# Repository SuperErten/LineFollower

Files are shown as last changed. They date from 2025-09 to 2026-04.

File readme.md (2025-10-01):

# LineFollower

lege repository die je als template kan gebruiken om een eigen repository te starten voor uw linefollower project

A description of my image


## specifications (Plan B)

microcontroller: ESP32 (Devkit V1)

motors: (50:1) micro metal gearbox HP 6V - pololu

h-bridge: DRV8833

sensors: QTR-8A

batteries: 18650 - 3.7x2V; 2.6A

wireless communication: See microcontroller

distance sensor - motors:

weight:

speed:

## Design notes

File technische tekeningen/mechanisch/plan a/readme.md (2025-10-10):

## Latest PCB design
<br />
Exported in DXF, 3D model (obj) and EASYEDA (json).

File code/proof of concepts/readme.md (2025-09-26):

# Proof of Concepts

Een proof of concept is een combinatie van minimale hard- en software om eenvoudig aan te tonen dat iets werkt.  
Proof of concepts kunnen enerzijds als eerste poging dienen om een bepaald onderdeel van het project werkend te krijgen. Anderzijds kunnen ze tijdens het debuggen van het finale project dienen als test om eventuele hardware problemen te elimineren bij onduidelijke problemen.
<br />  
<br />
Een proof of concept bestaat uit
* een elektronisch schema (indien van toepassing)
* minimale code om de voorop gestelde zaken te demonstreren
* minimale uitleg / aandachtspunten
<br />
De elektronische schakelingen van de proof of concepts komen bij voorkeur overeen met deze van de uiteindelijke linefollower, zodat de code zonder aanpassingen op het finale project kan draaien.

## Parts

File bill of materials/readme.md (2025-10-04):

## bill of materials Plan B
<br />

|volgnummer|naam|omschrijving|nieuw/recup|kostprijs/stuk|aantal|subtotaal|
|---|----|---|---|---|---|---|
| 1|ESP32 Devkit V1|Microcontroller|Recup|8,9 EUR|1|0 EUR|
| 2|Adafruit DRV8833|H-Brug DC motor driver|New|8,51 EUR|1|8,51 EUR|
| 3|QTR-8|Reflectance Sensor Array|New|10,96 EUR|1|10,96 EUR|
| 4|50:1 Micro Metal Gearbox HP 6V - Pololu|DC Motor|New|21,5 EUR|2|43 EUR|
| 5|DFR0205|Buck Converter (Step Down)|Recup|9,5 EUR|1|0 EUR|
| 6|Breadboard met 170 ronde gaten|Breadboard|Recup|4,9 EUR|2|0 EUR|
| 7|Batterijhouder - 2x18650|Batterij Houder|Recup|2,65 EUR|1|0 EUR|
| 8|2 x 18650|Batterij|Recup|2 EUR|2|0 EUR|
| 9|Pololu Wiel 80×10mm Paar|Wielen|New|7,9 EUR|1|7,9 EUR|
| 10|Ball Caster Pololu |Wiel|New|2,90 EUR|1|2,90 EUR|
| 11|Micro Metal Gearmotor Bracket Wit N20 paar |Motor Bracket|New|3,75 EUR|2|3,75 EUR|
| 12|Button Yellow |Button|Recup|0,1 EUR|1|0 EUR|
| 13|Jumper Kabels (Depont) |Wired|Recup|5 EUR|1|0 EUR|
| 14|Moertjes en Boutjes |Moerenen Bouten|Recup|1 EUR|1|0 EUR|
| 15| | | | |Totaal:|77,02 EUR|

## bill of materials Plan B - Goedkopere Alternatieve
<br />

|volgnummer|naam|omschrijving|Alternatief|kostprijs/stuk|Bespaart|
|---|----|---|---|---|---|
| 2|Adafruit DRV8833|H-Brug DC motor driver|CJMCU-8833, DRV8833|2,75 EUR|5,76 EUR|
| 3|QTR-8|Reflectance Sensor Array|HY-S301|3,5 EUR|7,46 EUR|
| 4|50:1 Micro Metal Gearbox HP 6V - Pololu|DC Motor|N20 Mini Micro Metal Gear Motor 6V 500 RPM|1,75 EUR|19,75 EUR|
| 5|DFR0205|Buck Converter (Step Down)|XL4015-B Breakout|1,45 EUR|8,05 EUR|

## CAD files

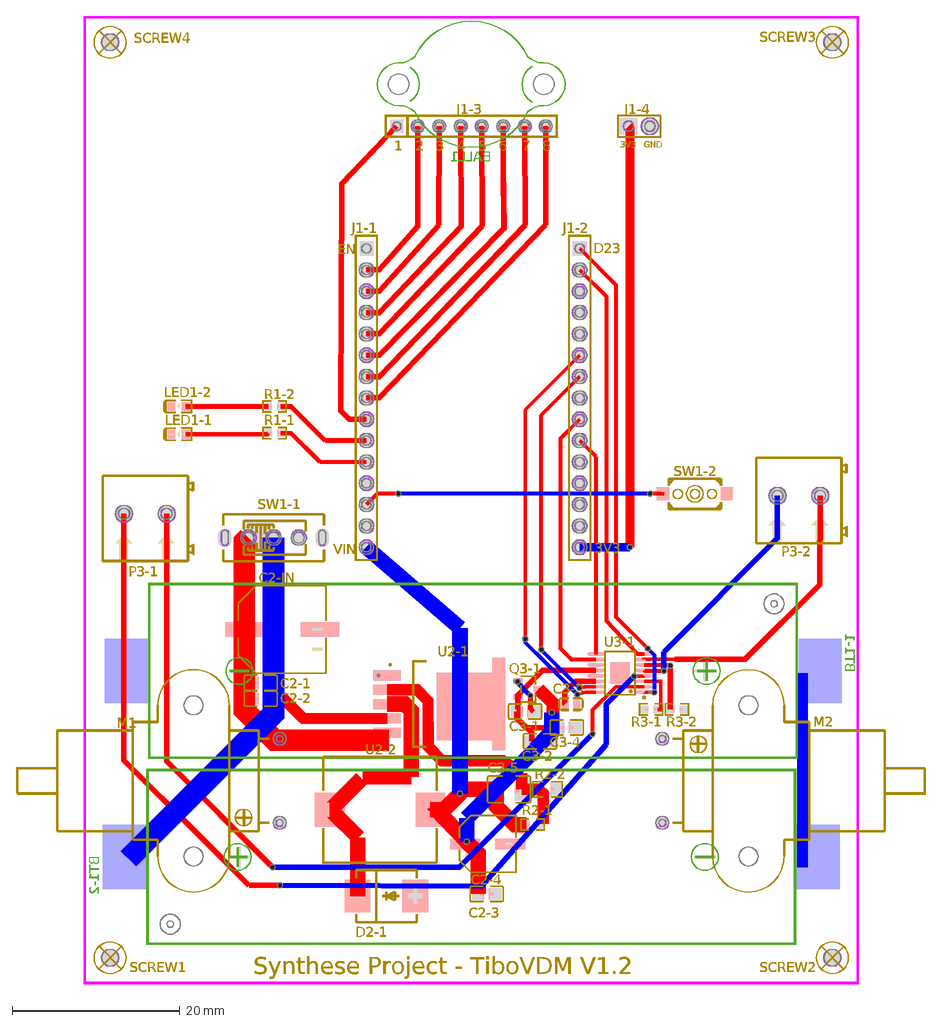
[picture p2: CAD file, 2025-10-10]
technische tekeningen/mechanisch/plan a/LineFollower_2025-10-10.dxf
Synthese Project - TiboVDM V1.2
1
2
3
4
5
6
7
8
3V3
GND
EN
D23
VIN
BT1-2
BT1-1
BALL1
J1-4
J1-3
C2-4
M1
M2
C2-1
C2-2
C2-3
C3-1
C3-2
C3-4
C2-5
C2-IN
C3-3
D2-1
LED1-1
LED1-2
P3-1
P3-2
Q3-1
R1-1
R1-2
R3-1
R3-2
R2-1
R2-2
SCREW1
SCREW2
SCREW3
SCREW4
SW1-1
SW1-2
J1-1
J1-2
U2-1
U2-2
U3-1

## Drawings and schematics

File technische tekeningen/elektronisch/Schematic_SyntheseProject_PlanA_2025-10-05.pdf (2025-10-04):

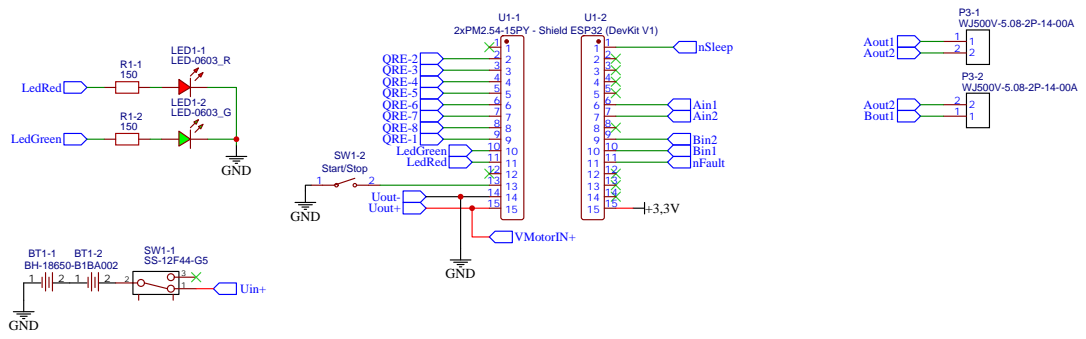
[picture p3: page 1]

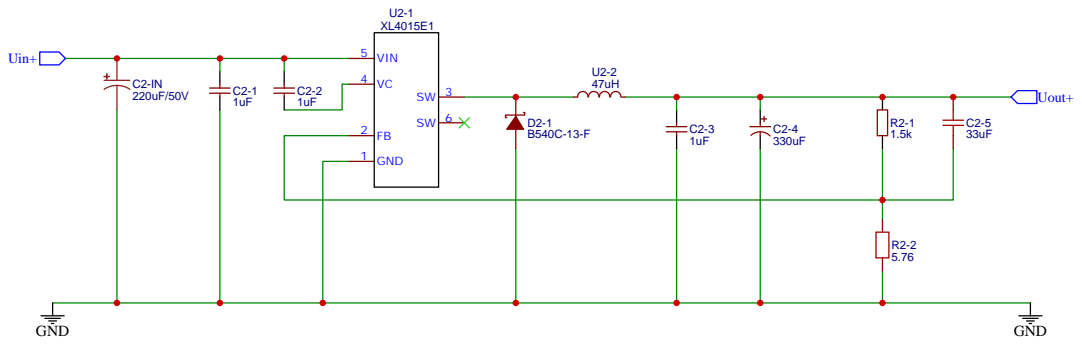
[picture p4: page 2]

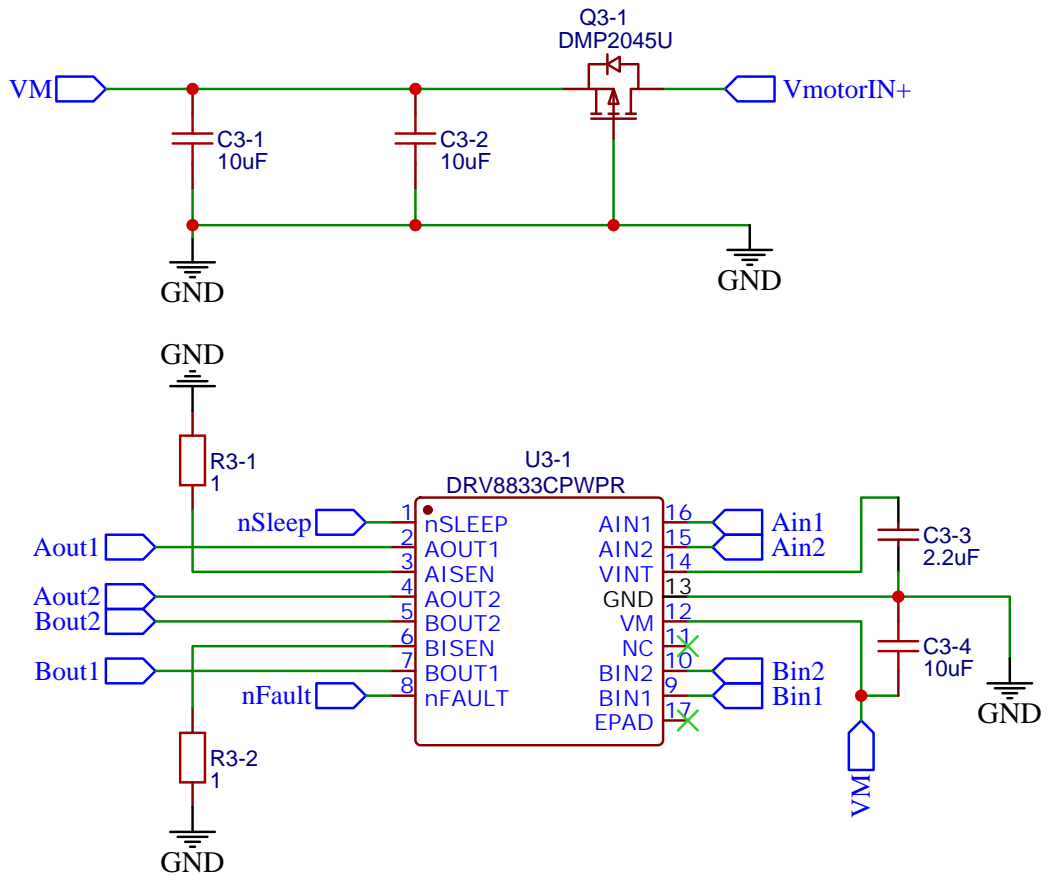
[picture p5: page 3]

BIN2 10 NC 11 VM 12 GND 13 VINT 14 AIN2 15 AIN1 16

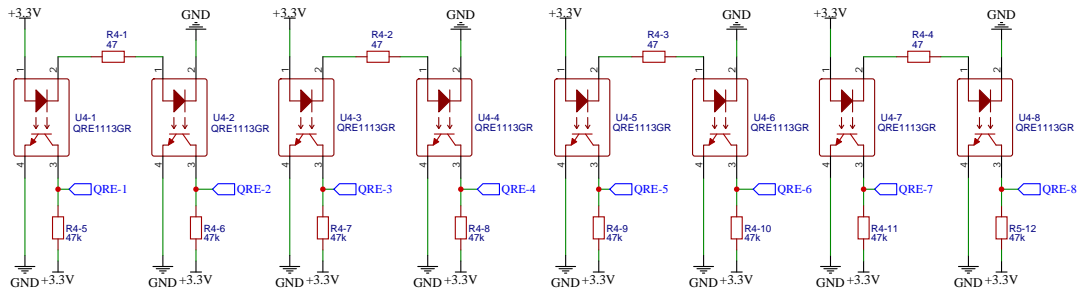
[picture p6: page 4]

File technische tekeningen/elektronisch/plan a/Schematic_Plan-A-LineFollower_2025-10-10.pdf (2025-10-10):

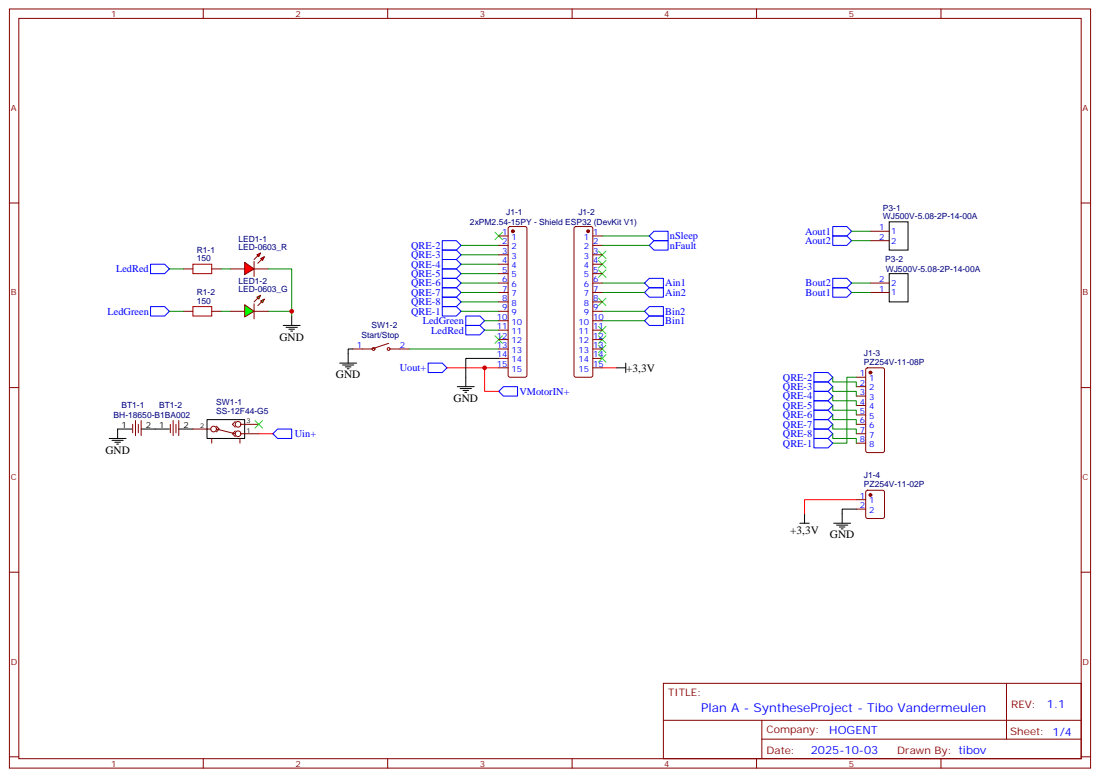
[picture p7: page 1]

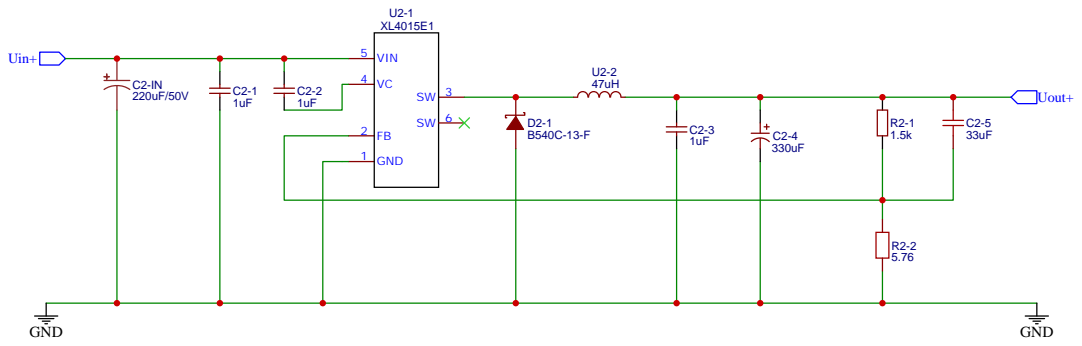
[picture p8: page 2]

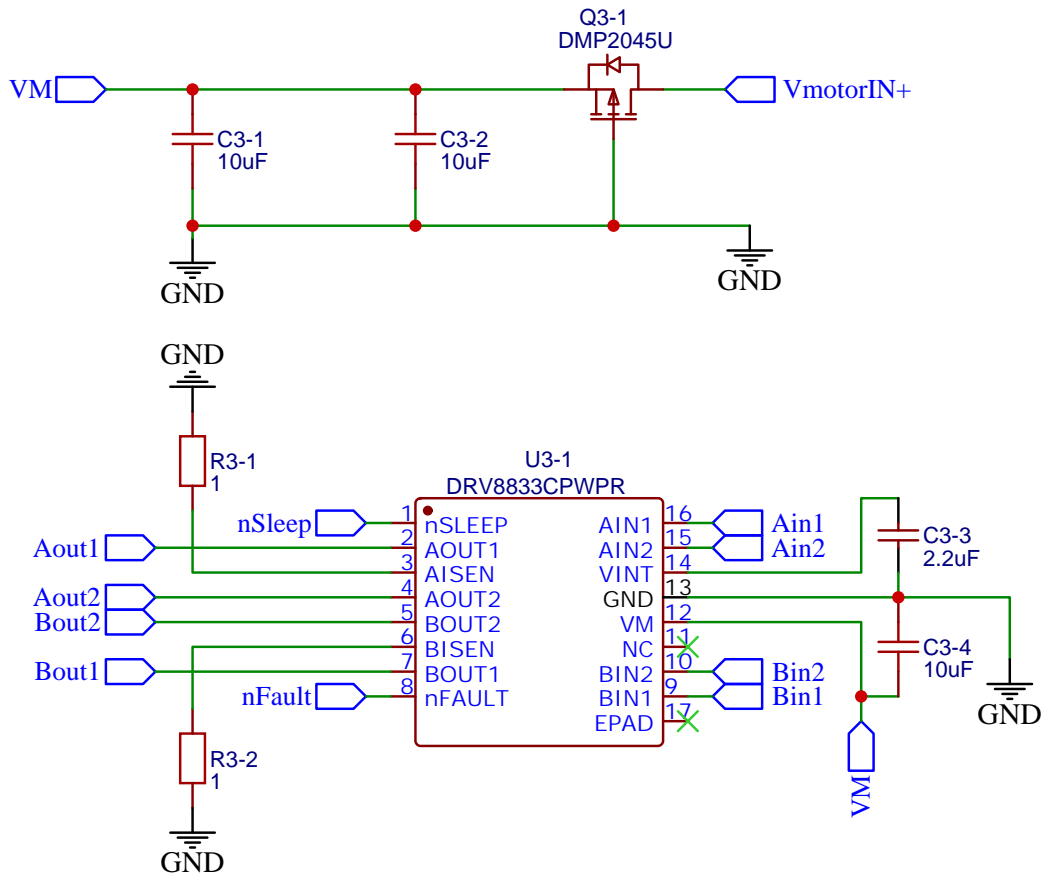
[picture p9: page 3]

BIN2 10 NC 11 VM 12 GND 13 VINT 14 AIN2 15 AIN1 16

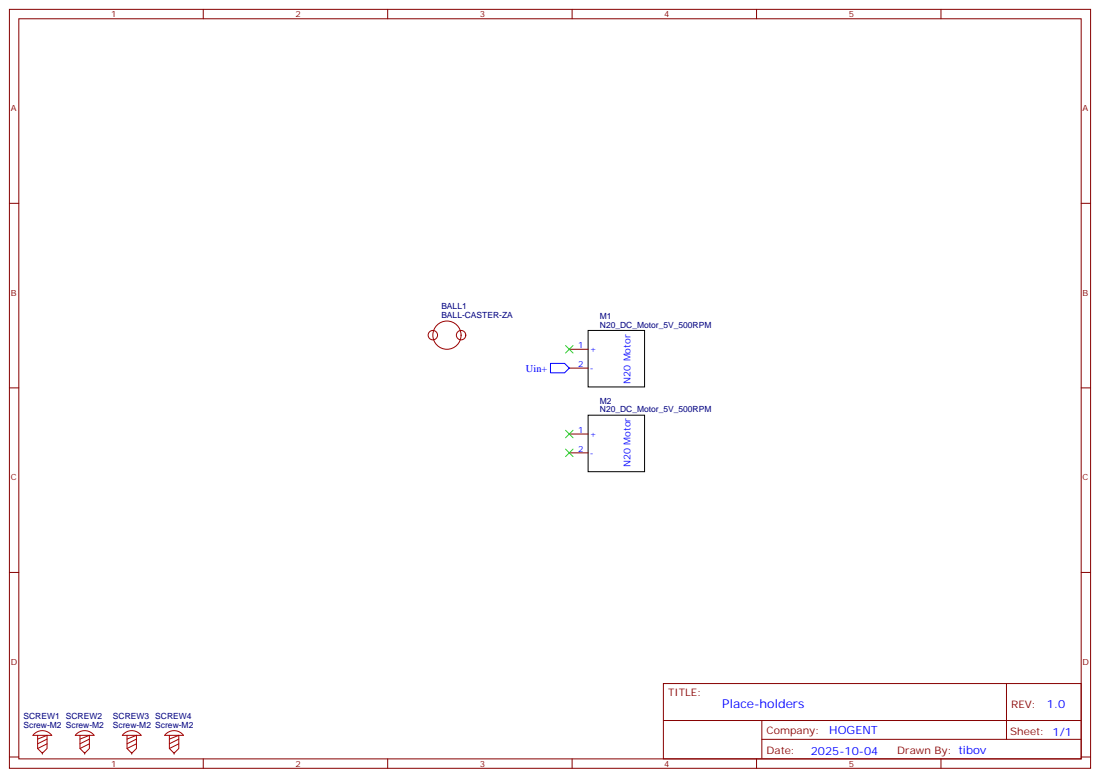
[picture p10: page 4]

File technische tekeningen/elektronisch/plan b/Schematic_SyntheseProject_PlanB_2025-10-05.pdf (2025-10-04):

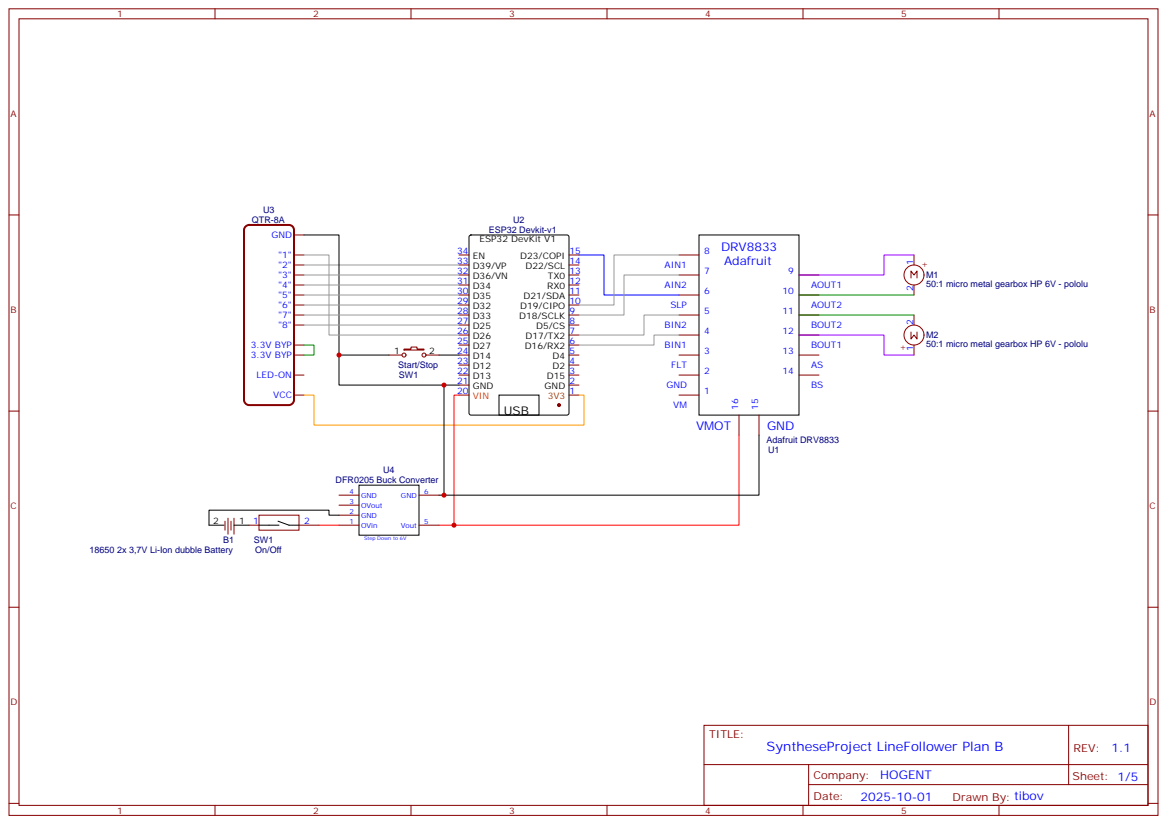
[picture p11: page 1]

D19/CIPO 10 D21/SDA 11 RX0 12 TX0 13 D22/SCL 14 D23/COPI 15

18650 2x 3,7V Li-Ion dubble Battery

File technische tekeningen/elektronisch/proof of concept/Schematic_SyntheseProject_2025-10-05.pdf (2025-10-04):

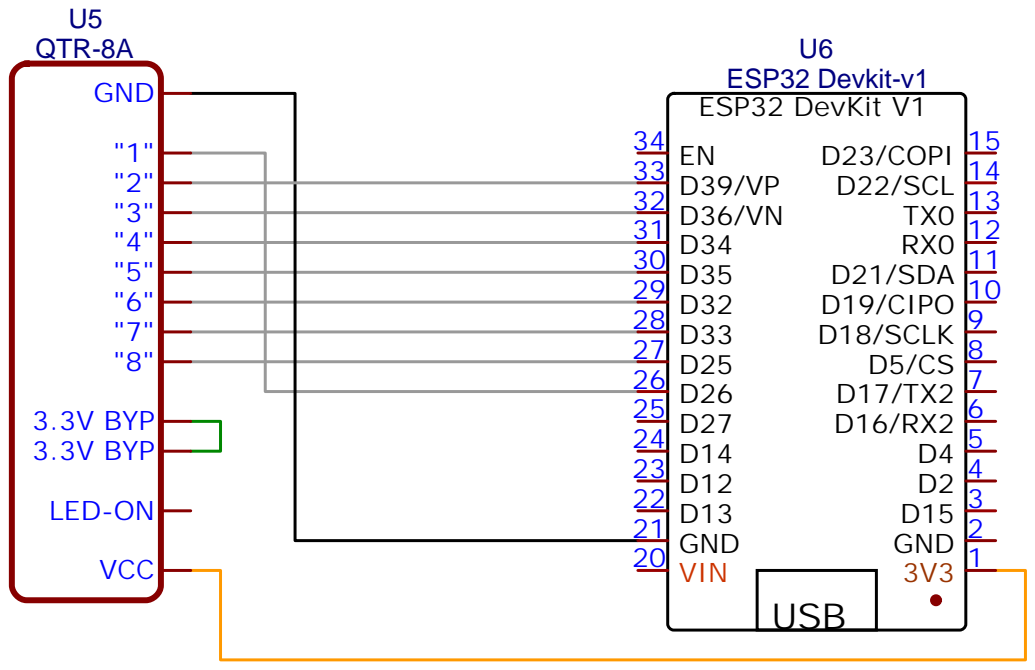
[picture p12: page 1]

D19/CIPO 10 D21/SDA 11 RX0 12 TX0 13 D22/SCL 14 D23/COPI 15

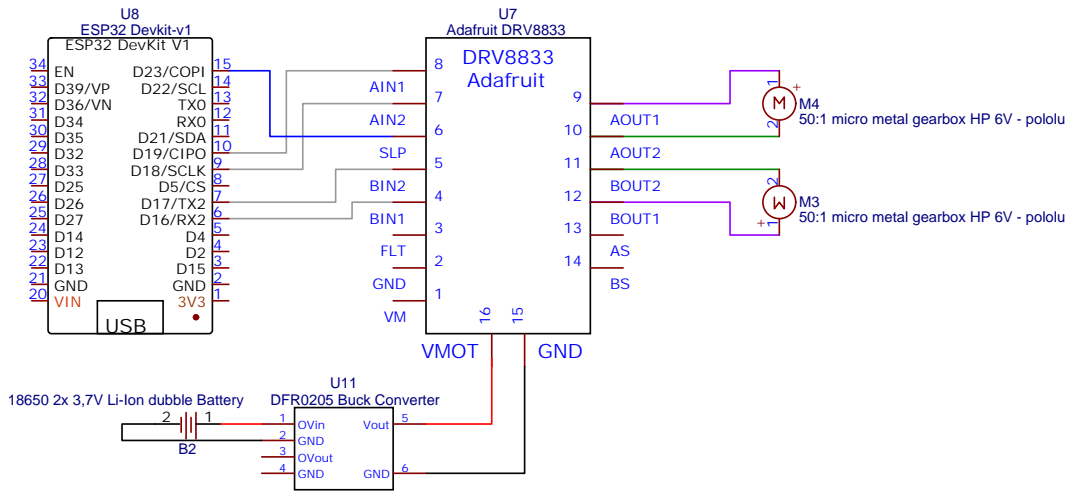
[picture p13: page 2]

D19/CIPO 10 D21/SDA 11 RX0 12 TX0 13 D22/SCL 14 D23/COPI 15

18650 2x 3,7V Li-Ion dubble Battery

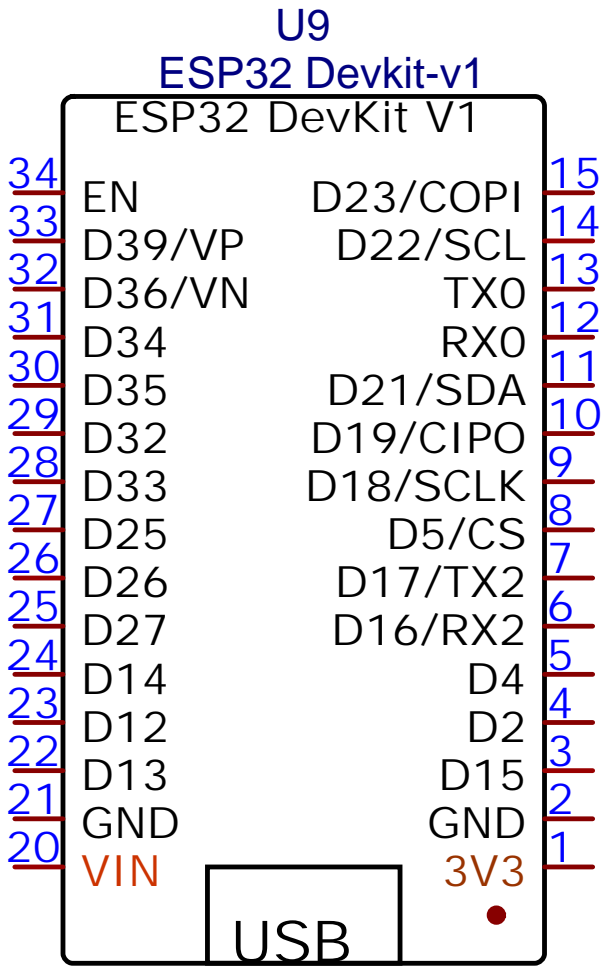
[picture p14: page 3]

D19/CIPO 10 D21/SDA 11 RX0 12 TX0 13 D22/SCL 14 D23/COPI 15


D19/CIPO 10 D21/SDA 11 RX0 12 TX0 13 D22/SCL 14 D23/COPI 15

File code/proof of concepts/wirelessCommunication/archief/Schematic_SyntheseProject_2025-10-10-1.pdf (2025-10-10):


Stappen Plan:
*Maak Hotspot met GSM (ssd: "Tibo123" psswrd: "876543210"
*Connecter met wifi, klik EN op ESP32 Devkit V1
* Ga naar webserver "10.11.154.32"

D19/CIPO 10 D21/SDA 11 RX0 12 TX0 13 D22/SCL 14 D23/COPI 15

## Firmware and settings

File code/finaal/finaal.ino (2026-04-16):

#include <WiFi.h>
#include "Cdrv8833.h"
#include <WebServer.h>
#include <QTRSensors.h>
#include <Preferences.h>
#include "freertos/task.h"
#include "driver/gptimer.h" 

constexpr uint8_t PIN_DI_START_STOP = 13;
constexpr uint8_t PIN_DO_LED_RED    = 14;
constexpr uint8_t PIN_DO_LED_GREEN  = 27;

QTRSensors qtr;
const uint8_t SensorCount = 8;
uint16_t sensorValues[SensorCount];

volatile bool interruptTriggerd = false;
volatile unsigned long lastDebounceTime = 0;
const unsigned long debounceDelay = 100; //ms

const char* ssid     = "Tibo123";
const char* password = "876543210";

volatile bool stateRobot = 0;
volatile float Kp = 0;
volatile float Ki = 0;
volatile float Kd = 0;

float P = 0, I = 0, D = 0;

unsigned long lastTime;
float inputPID, outputPID;
float ITerm, lastInputPID;
float outMinPID, outMaxPID;
float setpointPID = 4000;
int sampleTimePID = 15000; // 15 ms Sample Time

constexpr uint8_t PIN_AIN1          = 19;
constexpr uint8_t PIN_AIN2          = 18;
constexpr uint8_t CHANNEL_MOTOR_A   = 0;
constexpr bool SWAP_MOTOR_A         = 0;

constexpr uint8_t PIN_BIN1          = 16;
constexpr uint8_t PIN_BIN2          = 17;
constexpr uint8_t CHANNEL_MOTOR_B   = 1;
constexpr bool SWAP_MOTOR_B         = 0;

int baseSpeed = 35;          // basis vooruit (0..100)
int maxSpeed  = 80;          // clamp (0..100)

Preferences prefs;

WebServer server(80);

TaskHandle_t pid_compute_handle = NULL;

Cdrv8833 motorA(PIN_AIN1, PIN_AIN2, CHANNEL_MOTOR_A, SWAP_MOTOR_A);
Cdrv8833 motorB(PIN_BIN1, PIN_BIN2, CHANNEL_MOTOR_B, SWAP_MOTOR_B);

//Maar één core kan globaal data aanpassen.
portMUX_TYPE stateMux = portMUX_INITIALIZER_UNLOCKED;

void IRAM_ATTR toggleState() {

  interruptTriggerd = true;
}

static bool IRAM_ATTR timerCallback(gptimer_handle_t timer, const gptimer_alarm_event_data_t *edata, void *user_data) {

  BaseType_t higher_priority_woken = pdFALSE;
  vTaskNotifyGiveFromISR(pid_compute_handle, &higher_priority_woken);
  return higher_priority_woken == pdTRUE;
}

void updateLEDs() {

  digitalWrite(PIN_DO_LED_RED,   !stateRobot);
  digitalWrite(PIN_DO_LED_GREEN,  stateRobot);
}

void readValuesQTR() {

  uint16_t position = qtr.readLineBlack(sensorValues);
	
  portENTER_CRITICAL(&stateMux);
  inputPID = (float)position;
  portEXIT_CRITICAL(&stateMux)


  for (uint8_t i = 0; i < SensorCount; i++) //Later Verwijderen
  {
    Serial.print(sensorValues[i]);
    Serial.print('\t');
  }
  Serial.println(position);
}

void calibrateQTR() {

  digitalWrite(LED_BUILTIN, true);

  for (uint16_t i = 0; i < 400; i++)
  {
    qtr.calibrate();
  }
  digitalWrite(LED_BUILTIN, false); 
}

void SetOutputLimits(double Min, double Max)
{
   if(Min > Max) return;
   outMinPID = Min;
   outMaxPID = Max;
    
   if(outputPID > outMaxPID) outputPID = outMaxPID;
   else if(outputPID < outMinPID) outputPID = outMinPID;
 
   if(ITerm> outMaxPID) ITerm= outMaxPID;
   else if(ITerm< outMinPID) ITerm= outMinPID;
}

void pidCompute(void *pvParameters) {
	
  const float dt = sampleTimePID / 1000000.0f;
  
   while (true) {
    ulTaskNotifyTake(pdTRUE, portMAX_DELAY);
	  
    float input, setpoint, kp, ki, kd, outMin, outMax, iTerm, lastIn;
    portENTER_CRITICAL(&stateMux);
    input   = inputPID;
    setpoint= setpointPID;
    kp      = Kp;
    ki      = Ki;
    kd      = Kd;
    outMin  = outMinPID;
    outMax  = outMaxPID;
    iTerm   = ITerm;
    lastIn  = lastInputPID;
    portEXIT_CRITICAL(&stateMux);

    float error = setpoint - input;

    iTerm += (ki * error * dt);
    if (iTerm > outMax) iTerm = outMax;
    else if (iTerm < outMin) iTerm = outMin;

    
    float dInput = (input - lastIn) / dt;

    float out = kp * error + iTerm - kd * dInput;
    if (out > outMax) out = outMax;
    else if (out < outMin) out = outMin;
    
    
    portENTER_CRITICAL(&stateMux);
    ITerm        = iTerm;
    outputPID    = out;
    lastInputPID = input;
    portEXIT_CRITICAL(&stateMux);
   }
}

void setup() {

  Serial.begin(115200);

  prefs.begin("pid", false);
  Kp = prefs.getFloat("Kp", 0.0);
  Ki = prefs.getFloat("Ki", 0.0);
  Kd = prefs.getFloat("Kd", 0.0);
  prefs.end(); 
  
  pinMode(PIN_DI_START_STOP, INPUT_PULLUP);
  pinMode(PIN_DO_LED_GREEN, OUTPUT);
  pinMode(PIN_DO_LED_RED , OUTPUT);
  pinMode(LED_BUILTIN, OUTPUT);
  
  motorA.setDecayMode(drv8833DecayFast);
  motorB.setDecayMode(drv8833DecayFast);
  
  qtr.setTypeAnalog();
  qtr.setSensorPins((const uint8_t[]){26, 36, 39, 34, 35, 32, 33, 25}, SensorCount); // 

  attachInterrupt(digitalPinToInterrupt(PIN_DI_START_STOP), toggleState, FALLING);
  updateLEDs();

  // draaien op 2 aparte core's wifi o en main op 1
  xTaskCreatePinnedToCore(wifiLoop,  "wifiLoop",  8192, NULL, 1, NULL, 0);
  xTaskCreatePinnedToCore(mainLoop, "mainLoop", 4096, NULL, 1, NULL, 1);
  // Ineterupt task voor PID om tijd zo stabiel mogelijk te maken
  xTaskCreatePinnedToCore(pidCompute, "pidCompute", 4096, NULL, 5, &pid_compute_handle, 1);

  // timer voor intterupt
  gptimer_handle_t timer = NULL;

  gptimer_config_t timer_config = {};
  timer_config.clk_src = GPTIMER_CLK_SRC_DEFAULT;
  timer_config.direction = GPTIMER_COUNT_UP;
  timer_config.resolution_hz = 1000000;
  gptimer_new_timer(&timer_config, &timer);

  gptimer_alarm_config_t alarm_config = {};
  alarm_config.alarm_count = sampleTimePID;
  alarm_config.reload_count = 0;
  alarm_config.flags.auto_reload_on_alarm = true;
  gptimer_set_alarm_action(timer, &alarm_config);

  gptimer_event_callbacks_t cbs = {};
  cbs.on_alarm = timerCallback;
  gptimer_register_event_callbacks(timer, &cbs, NULL);

  gptimer_enable(timer);
  gptimer_start(timer);
}

void mainLoop(void* pvParameters) {
  while (true) {
    if (interruptTriggerd) {
      interruptTriggerd = false;
      unsigned long now = millis();

      if (now - lastDebounceTime > debounceDelay) {
        lastDebounceTime = now;
        portENTER_CRITICAL(&stateMux);
        stateRobot = !stateRobot;
		
		if (!stateRobot) {
		  ITerm = 0;
		  outputPID = 0;
		  lastInputPID = inputPID;
		}
        portEXIT_CRITICAL(&stateMux);

        updateLEDs();
      }
    }

    if (stateRobot) {
      readValuesQTR();
	  
	  float out;
      portENTER_CRITICAL(&stateMux);
      out = outputPID;
      portEXIT_CRITICAL(&stateMux);
	  
	  float steer = (out / 255.0f) * 100.0f;
	  
	  int left  = (int)roundf(baseSpeed + steer);
	  int right = (int)roundf(baseSpeed - steer);
	  
	  left  = constrain(left,  -maxSpeed, maxSpeed);
	  right = constrain(right, -maxSpeed, maxSpeed);
	  
      motorA.move((int8_t)left); 
      motorB.move((int8_t)right);  
    }
	else {
	  motorA.brake();
	  motorB.brake();
	}
	vTaskDelay(1 / portTICK_PERIOD_MS);
  }
}

void loop() {
}

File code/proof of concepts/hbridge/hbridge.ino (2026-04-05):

#include "Cdrv8833.h"

constexpr uint8_t PIN_AIN1          = 19;
constexpr uint8_t PIN_AIN2          = 18;
constexpr uint8_t CHANNEL_MOTOR_A   = 0;
constexpr bool SWAP_MOTOR_A         = 0;

constexpr uint8_t PIN_BIN1          = 16;
constexpr uint8_t PIN_BIN2          = 17;
constexpr uint8_t CHANNEL_MOTOR_B   = 1;
constexpr bool SWAP_MOTOR_B         = 0;

Cdrv8833 motorA(PIN_AIN1, PIN_AIN2, CHANNEL_MOTOR_A, SWAP_MOTOR_A);
Cdrv8833 motorB(PIN_BIN1, PIN_BIN2, CHANNEL_MOTOR_B, SWAP_MOTOR_B);

void setup()
{
    Serial.begin(115200);
    Serial.println("\n");
    Serial.println("DRV8833 tester");
    Serial.println("--------------");
    Serial.printf("IN1 pin: %u\nIN2 pin: %u\n\n", IN1_PIN, IN2_PIN);

    Serial.println("SWAP    - swap motor rotation direction.");
    Serial.println("NOSWAP  - restore motor rotation direction.");
    Serial.println("SLOW    - decay mode SLOW - good torque, high power consumption.");
    Serial.println("FAST    - decay mode FAST - poor torque, low power consumption.");
    Serial.println("MOVEXXX - start rotation (XXX = -100..100).");
    Serial.println("STOP    - stop the motor.");
}

void loop()
{
    String command;
    if (Serial.available()) { // check Serial for new command
        command = Serial.readString(); // read the new command from Serial
        command.toLowerCase(); // convert it to lowercase

        if (command.equals("swap")) {
            motorA.swapDirection(true); // swap rotation direction
            Serial.println("--> swapped rotation direction.");
        }
        else if (command.equals("noswap")) {
            motorA.swapDirection(false); // default rotation direction
            Serial.println("--> default rotation direction.");
        }
        else if (command.equals("slow")) {
            motorA.setDecayMode(drv8833DecaySlow); // decay mode SLOW
            Serial.println("--> Decay mode SLOW - good torque.");
        }
        else if (command.equals("fast")) {
            motorA.setDecayMode(drv8833DecayFast); // decay mode FAST
            Serial.println("--> Decay mode FAST - poor torque.");
        }
        else if (command.equals("stop")) {
            motorA.stop(); // stop moto rotation
            Serial.println("--> Motor stopped.");
        }
        else if (command.startsWith("move")) {
            command.replace("move", ""); // remove the word "move"
            command.replace(" ", "");    // remove spaces (if present)
            motorA.move(command.toInt()); // start rotation at desired speed
            Serial.printf("--> Motor rotation speed: %ld.\n", command.toInt());
        }
    }
}

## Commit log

2025-10-04 Update readme.md
    Added BOM
2026-04-04 added Sensor
2026-04-05 Wireless comunicatie herschreven nu draai webserver op core 0, en robot op core 1
2026-04-05 Added Finaal en GPU/Timer voor interupt PID
2026-04-15 PID toegevoegd
